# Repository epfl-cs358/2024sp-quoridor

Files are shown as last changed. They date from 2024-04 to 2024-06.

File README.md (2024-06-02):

# 2024sp-quoridor

# Project overview

This project aims to create a modified version of the physical board game called Quoridor, a strategic maze-building game, where a player competes against a computer opponent on the board. <br> 
Quoridor is a 2 player game where each player’s piece start on opposite sides of the board, each turn the player chooses to either move their piece in any cardinal direction (up, down, left, right) or place a wall to block the other player’s path (walls cannot be moved once placed), the first player to get to the other side wins. 

# Project Proposal link:

https://docs.google.com/document/d/114cAhuUHxiCxB0LIXvpHFLx6ZjFtf0oyKlaDsvuiIQ8/edit?usp=sharing

# Project instructions
These instructions are structured in 2 sub-assemblies:
- The Gripper
  
- The machine
  - Main part
  - Y axis rail
 
As well as a set of instructions for the Computer Vision:
- Players and walls detection
- Game board and coordinates building

The two sub assemblies can be built in parallel and assembled at the end. The design is such that only two screws hold the gripper to the rest of the assembly, so it's quite easy to modify the gripper seperately.

# Gripper
## Overview:
Here is the design of the gripper for the Quoridor game board.
The gripper's movements include rotation (±280°), translation (10 cm), and gripping (4 cm wide). The gripper is powered by two DMS15 motors and one Servo 9G, with a power supply of 5V from an external source, drawing a maximum of 3A.

Gripper CAD

Gripper CAD Back

Gripper CAD

Gripper CAD

Gripper CAD

## Required Components:
Motors:
- 2x DMS15 Servo
- 1x 9G Servo

Bearings:
- 2 dry bearings (outer diameter: 10mm, inner diameter: 8mm)
- 1 standard bearing (outer diameter: 24mm, inner diameter: 15mm)
- 2 Metal Shafts 100x8mm

Tools: File, lubricant, screwdriver

Equipment: 3D printer, laser cutter (for plates of 5mm and 3mm thickness, or alternatively, these parts can be 3D printed) 

## Assembly Instructions:
#### Gripper Assembly:

1. Clean the gear and the two racks with the file.
2. Attach the claws to the claw racks using screws (two screws per claw). Ensure the screws are tightened sufficiently to prevent any movement.
3. Mount the gear onto the servo. Apply a bit of force to fit it securely and then screw it in place (Note: This servo is trash).
4. Slide the two claws onto the rack holder, positioning them close together.
5. Use an Arduino to run the servo, setting it to its maximum position (180° = closed).
6. Slide the servo on top of the rack holder. Adjust the claws slightly to ensure the teeth align correctly (this step may require some patience, precision and despair).
7. Optional: you can stick pieces of rubber on the gripper clamp to increase adhesion (I used pieces of rubber glove).

Gripper CAD
Gripper CAD
Gripper CAD
Gripper CAD

#### Moving Part:

1. Clean the bearing holder and the main linear part.
2. Insert the bearing and nuts into the bearing holder.
3. Mount the servo on top of the bearing holder.

Gripper CAD

5. Insert the two dry bearings and nuts into the main linear part.
6. Position the servo with the bearing holder underneath the main linear part.
7. Secure the assembly by adding screws to the top of the main linear part. Use a small screwdriver to access the holes.
8. Slide the rack under the rack holder.
9. Attach the rack holder to the back of the main linear part, ensuring the rack holder protrudes upwards.

#### Main Part:

1. Try to pass the 2 metal axes through the two laser-cut 5mm parts. If necessary, use a file to clean the holes, but do not over-file as the axes need to stay securely in place.
2. Place the left and right pillar supports on the 5mm main plate. You can add screws for additional stability, but this is not mandatory.
3. Position the two upper pillar fix on top of the pillar spacers and screw them in place.
4. Place nuts on the right pillar support and the linear servo support, then screw them onto the main plate.
5. Attach the servo circular extender (I dont know how to call that) to the main gear and secure it using the screws provided with the servo.
6. Insert the two metal axes, slide the moving part onto them, and add the two spacers at the top.

Gripper CAD

8. Position the servo motor and the two pillars, then add screws at the top and base to secure them.
9. Run the two servos with an Arduino, ensuring the rotation is set to 0 and the linear position is also at 0.
10. Attach the main lower plate to the main plate using spacers.
11. Slide the moving part to the top and fix the gear onto the servo motor. The goal is to have the last teeth of the rack engaged by the gear. (Optional: It is recommended to screw it only when everything is installed).
12. Return to the claw assembly. Fix the gripper support servo to the bearing, applying a bit of force to secure it, and add the screws provided with the servo.
13. Insert the servo from the claw into the gripper support servo, ensuring the cables are passed through before positioning the servo. 
14. Add two screws to secure everything. (Optional: It is recommended to do this only when everything is installed and tested to avoid damaging the claw).

## Wiring:

Due to their high power consumption, all 3 servos must be powered by an external power source of at least 5v/3amp.
Here is the electrical diagram to connect them to a Ramps 1.6



1 is the gripper servo, 2 is the rotation servo and 3 is the servo of the linear actuator.

Wiring
Wiring
Wiring

## Improvements:

- The 9G servos are unreliable and prone to malfunction. Consider using higher-quality or bigger servos to improve the performance and longevity of the gripper.

# Machine sub-assembly



# 3D printed parts

## Camera mount
- 1x main part
- 1x camera clamp


## Walls

- 10x in red
- 10x in blue

  Print in this direction to get the best results (no supports necessary)
2024-05-30-134702_1920x1080_scrot

## Player pawns

- 1x in red
- 1x in blue

## Board

- 2x "long"
  

- 1x "square"
  

- 1x "little square"
  

## Angle brackets
- 15x
2024-05-30-134950_1920x1080_scrot

## Corner brackets

Warning, these are symetrical pieces !
One of each
2024-05-30-135919_1920x1080_scrot

## End pulley

- 2x


## Optionnal : 3D printed T-nuts

The metallic openbuilds t-nuts are recommended. We 3d printed those because we forgot to order them. We ended up doing a slightly modified version of the original openbuilds CAD model with a bigger diameter, that works better when 3d printing
2024-05-30-135202_1920x1080_scrot

# Laser cutting

## In MDF

## Main board
- 1x Main board, 10mm

## Walls holder
- 2x, 3mm

## In acrylic

## Camera arms
- 2x, 5mm 


## Wheel plate
-3x 3mm
2024-05-30-143234_1920x1080_scrot

## Stepper mount plate
-2x 3mm


## End pulley bracket

- 4x 3mm (Two are used per axis)


## What needs improvements

3mm thick acrylic is not strong enough. We had a failure for an end pulley bracket, the 3d printed part ended up stronger.
signal-2024-05-30-124640

We also a noticed a crack developing on one of the wheel plate
signal-2024-05-30-124415

# Assembly instructions

With all the parts cut and printed, we are ready for assembly (note that you can also 3d print as you go, since the three pieces for the board for example take quite long to print)

First, screw in the wall holders pieces to the board. These parts add thickness to the board, so doing this first helps stabilizing it a bit more (MDF tends to bend with time).
2024-05-30-140227_1920x1080_scrot

Next, screw in the 8 angle brackets to the board (4 on each side).


Attach the V slot aluminium profiles, screwing them in place with the t-nuts

Screw in the corner brackets. These help stabilizing the profiles, and at the end to mount the camera arms.


Now flip the board upside down, with the top side of the profile resting on your workspace. We will use the profile as spacer.
Slide in the 3d printed boards part. Glue them. gravity will hold them in place. We used fast super-glue, but with this setup you can use a glue that takes a while to set.


## X axis assembly (built this seperately)

Warning : follow precisely this order, so you don't need to dissassemble sub-assemblies down the line

Mount the wheels to the wheel plate (this is the plate we will later mount the gripper to)
Slide the wheels+plate assembly to the middle of the profile.

Mount the end pulley plates on both side on end of the profile


Mount the stepper mounting plate on the other side
WhatsApp Image 2024-05-30 at 15 28 48

Mount the angle bracket to the v-slot. The placement is simple : on each end,  they are next to each other, sarting at the end of the profile.

### Do this two times, for both sides:

Mount the wheels to the plate and then slide the assembled carriage.



## Combine x axis assembly with the rest
Now we can mount the stepper on the x axis with the belt. Attach the belt to the plate going above the profile like this:

signal-2024-05-30-131015

Slide in the end switch mount. Tighten it so it does not move, but don't try to be precise with regards to the adjustments. Adjustements are done when everything is in place.

9f54f568-a379-4a69-852f-7c88d7756aae

Attach the Y stepper to the stepper motor plate, setup the belt but don't attach it to the gripper plate yet.

Put the gripper assembly on top of the plate, screw it in place


Screw in the electronic box.
Put the arduino+ramps+motor driver sandwich inside of it. Do the wiring according to the diagram. Pass the cables via the side holes (otherwise you won't be able to close the lid at the end).

335123297-452fb32d-1a28-4367-88d5-c3750ed1e14c (1) (1) (1)

## Camera arms

1. Screw in the arms to the angle brackets
WhatsApp Image 2024-05-30 at 14 55 10

2. Connect bot arms together


3. Mount the camera using the clamp
e45bf986-da7e-4e04-8ccc-194e948133e6

## Button

1. Screw in the button housing to the board
2. screw the button itself to the housing from below



## The end

Congratulation ! At this point, you should have the full machine assembled like this:


You can now proceed with adjustements regarding the end switch positioning, as well as the camera angle for the webcam.

# Arduino code 
The arduino code is separated in 2 parts, one is for all movements on the board (the X, Y axis stepper motors and 3 servo motors for the gripper) and the part is for communication and interpreter which will send, receive and decode message from the computer which it will translate to valid moves on the board. <br> <br>

The arduino will be managing communication with itself and the computer with a serial connection.
This diagram shows the communication between all of our components: <br> <br>


The arduino will send a "end turn" message through the serial once the button pressed, then the computer will communicate with the camera to detect the current board state (placement of the player pieces and the walls), with that it will compute the best move for the bot. Finally it will send the move information as the board position of the piece we want to grab, the new board position where we want to place the piece, the piece type, and optionally the orientation of the piece if it is a wall. <br> <br>

To accomplish the first part the arduino will stay idle, but once the player presses the end turn button it will trigger an interrupt. This will cause the arduino to print the message "get next move", which will be sent by the serial port. <br> <br>
Then the arduino will remain idle until it receives the move information from the computer.<br>
There are 2 types of moves, moving a player piece or a wall piece.
If the move is to move a player piece, then the move information will be under this form: <old_position><new_position><player> where old_position and new_position are board position for player pieces which are shown here:

<br> 
If the move is to move a wall piece, then the move information will be under this form: <old_position><new_position><wall><old_orientation><new_orientation> where old_orientation new_orientation are either horizontal or vertical, and old_position and new_position are board position for wall pieces which are shown here:

With all of this information the arduino knows what it has to do.<br> <br> 

Now for actually placing the piece where it needs to go. <br>
First we must move to the piece we desire to move, which we use the 2 X and Y stepper motors. Since the board was made with cells that are 4 times bigger than the gap between cells, it just takes knowing the distance in steps from the position 0 0 of the grabber to board position 00 for a player piece, and the distance in steps from a board position to a neighboring one board position to know how to move any board position for player pieces and wall pieces.<br>
That is the hard part done, then the gripper drops down, grabs the piece, pulls it back up, rotates it if it is needed (for instance if we had to place a vertical wall), moves to the new position, drops down, releases the piece, goes back up and moves back to its origin.<br><br>
Here are some videos that process working flawlessly:
<video src="https://github.com/epfl-cs358/2024sp-quoridor/assets/125994939/afad0169-728d-4bf2-bb4c-040145c0d592" controls></video>
<video src="https://github.com/epfl-cs358/2024sp-quoridor/assets/125994939/391f769e-7cd7-4f65-ab67-2949c7b72846" controls></video>

<br>

# Quoridor Solver
We implemented a greedy version of a Quoridor solver.
The solver sees the game as a graph where:
  - each board cell is vertex (with a board position attached to it).
  - each possibility of movement from one cell to another is represented by an edge from that vertex to the other.
  - each wall is represented by missing edges from 2 cells to 2 other cells.
<!--stop list--> 
The solver works as follows:
  - computes the shortest path to get to the other side for both players, it uses a breadth first search algorithm to do this, as it guarantees that it will find the shortest path first.
  - if the path of the robot is shorter than or equal to the one for the real player
    - then the robot is in an "advantaged" position, thus moves his player piece one step forward on its shortest path
  - otherwise it means the path of the robot is longer than the one for the real player
  - the robot is in a "disadvantaged" position, thus it will need to place a wall on the board if it wants to win
  - if the robot has 0 free walls to move:
    - there is nothing it can do to win, thus moves his player piece one step forward on its shortest path
  - else
    - for each wall position that goes on the real player's previously calculated shortest path:
      - checks that there is no colision with other walls on that board position
      - calculates the shortest path for both players on that new board with that wall placed
      - checks that there is a path to a winning cell for both players
      - keeps state of the best "winning move" and the best "losing move"
      - the best "winning move" is defined as the move that maximizes the distance difference between the robot's and player's new path where the robot's new path is the shorter one.
      - the best "losing move" is defined as the move that minimizes the distance difference between the robot's and the player's new path where the robot's new path is the longer one.
    - if a "winning move" exists:
      - it moves a free wall to the position in the best winning move
    - else
      - it moves a free wall to the position in the best losing move
<!--stop list-->
The solver seems quite robust and plays really well, but it still has some weaknesses due to the fact that it uses a greedy algorithm which means that it only considers the best move for itself on this turn. <br> 
So no future planning or strategy is going on and it won't consider what the real player can do in their future moves.

# Computer Vision
## Pieces detection
The playing pieces (players and walls) are recognized through color detection.

Using colorimetry software, we first get the BGR (Blue Green Red) color of each of the playing pieces we need to detect. This value, along with the camera feed, is then converted into the HSV (Hue, Saturation, Value) format. We now create a color mask based on the detected color with a range on the hue based on a sensitivity chosen to be 50 to account for the shadows and slight color variations.

Once we obtain this mask, we use OpenCV's minAreaRect function to obtain all the possible rectangles containing objects of the same color. We then apply filters to only keep the rectangles for which the height and width would correspond to our playing pieces. This is also how we distinguish between walls and player pieces since their enclosing rectangles would have different sizes.

Once we filter the rectangles of the correct sizes, we extract the centers of these rectangles which we then use to detect their coordinates on the grid. This part will be explained on the next section.

Finally, for the walls, we also need to detect their orientation. We do that using the "angle" value returned by the minAreaRect function and by comparing the width and height of the rectangle. Just the angle is not enough in our case since the openCV function returns a value between 0° and 90°,it is very error-prone when thresholding between Horizontal and Vertical values (if the value is slightly above 90°, it goes back again to 1°).

## Game board
The board, its cells, and wall gaps are not detected as is, but rather re-created after detecting the board's corners.
Each corner is uniquely identified by ArUco markers: they are a sort of QR code that can be generated and identified through its corresponding library.
Given the corners and the cells' number and dimensions, a grid is recreated: <br>
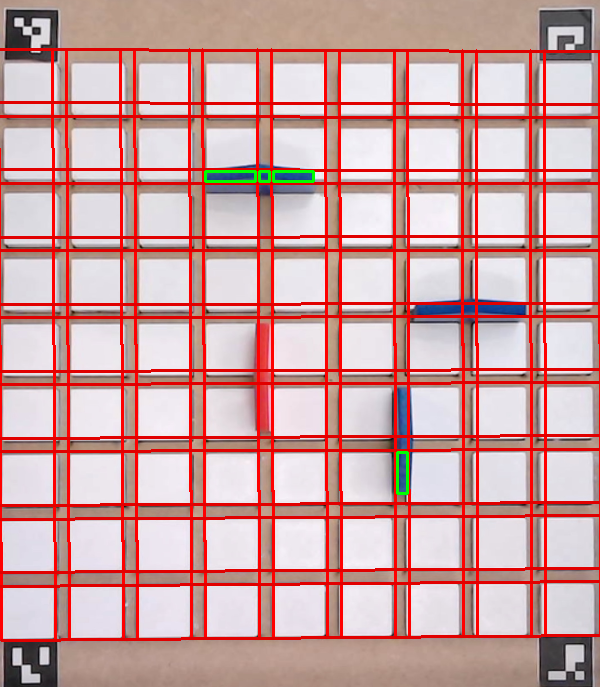
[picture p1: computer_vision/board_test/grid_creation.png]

<br> <br>
You can see in the picture that the grid is purposefully offset near the top. Because the camera is not directly centered on top of the board, walls near the top will tend to look like they are higher on the board than they truly are.
You will find more detail on aruco detection and perspective wrapping in the code /computer_vision/create_grid.py <br>
When creating the grid, the set of intersections between all perpendicular grid lines is stored for future use. For each intersection, we store the absolute coordinates as well as the game-system coordinates (9 units on each side, origin is bottom left) <br>
Then, given the absolute coordinates for the pieces' centers, the code uses the set of intersection coordinates to output, for the solver to use, the game-system coordinates of each piece. <br> <br>
When sticking the ArUco markers on the board, you should be mindful that the outer corners should be well-aligned with the board's corners (PS: the markers don't need to have the same size, they should just be well-aligned). <br>
Be careful however that they can be seen entirely from the camera (black square included). Here are corner-case examples: <br>
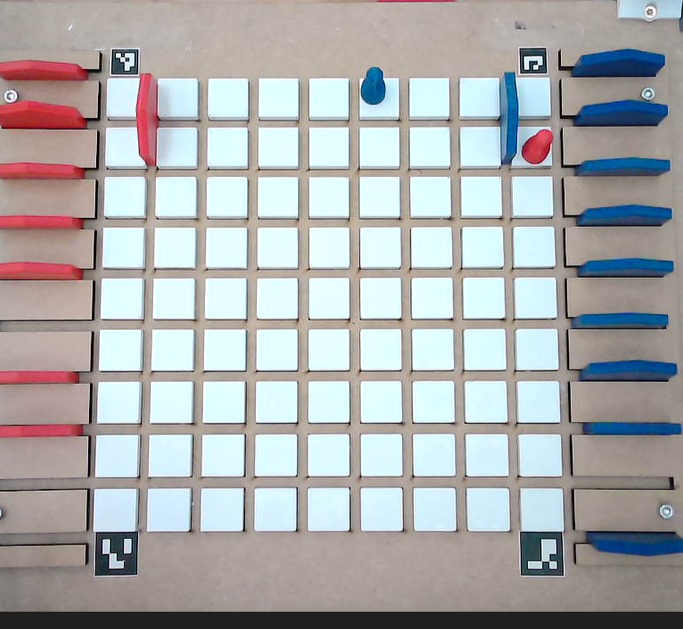
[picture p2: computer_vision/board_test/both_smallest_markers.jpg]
 <br>
On the image above, the top markers should be small enough that the walls placed at the top don't block them
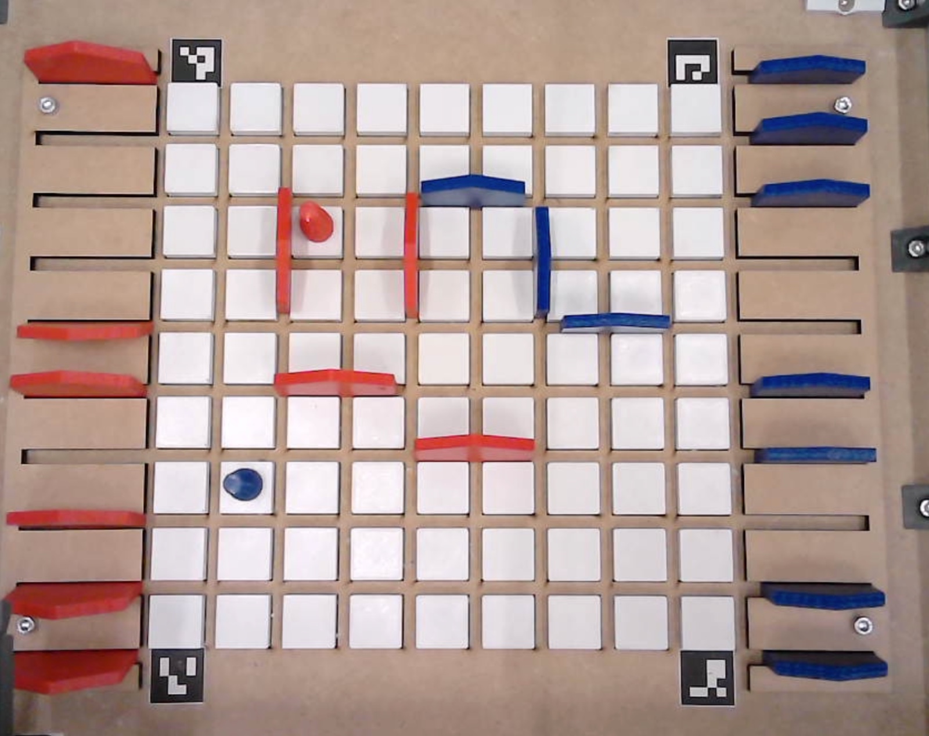
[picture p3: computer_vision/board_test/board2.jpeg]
 <br>
On the image above, the markers are too far down: the black square isn't showing entirely. <br> <br>

# Final Project
And that's it! <br> 
You have successfully built a Quoridor playing robot.<br> 
Now take seat and try to beat your new creation!<br>
<br>
Here you can check out some [videos](https://github.com/epfl-cs358/2024sp-quoridor/tree/main/videos) showing our project's successes (and failures) <br>
<video src="https://github.com/epfl-cs358/2024sp-quoridor/tree/main/videos/video1.mp4" controls></video>
<video src="https://github.com/epfl-cs358/2024sp-quoridor/tree/main/videos/video2.mp4" controls></video>
<video src="https://github.com/epfl-cs358/2024sp-quoridor/tree/main/videos/video3.mp4" controls></video>
<video src="https://github.com/epfl-cs358/2024sp-quoridor/tree/main/videos/video4.mp4" controls></video>

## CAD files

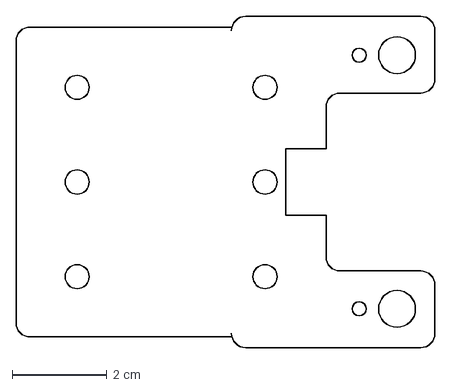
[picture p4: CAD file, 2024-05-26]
Gripper/Laser Cutting/Main plate.dxf
8.85 x 7.00 cm

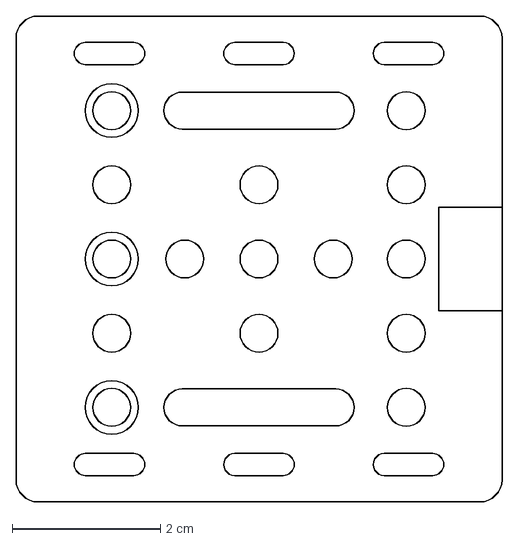
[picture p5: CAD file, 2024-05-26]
Gripper/Laser Cutting/Main Lower Plate.dxf
6.55 x 6.55 cm

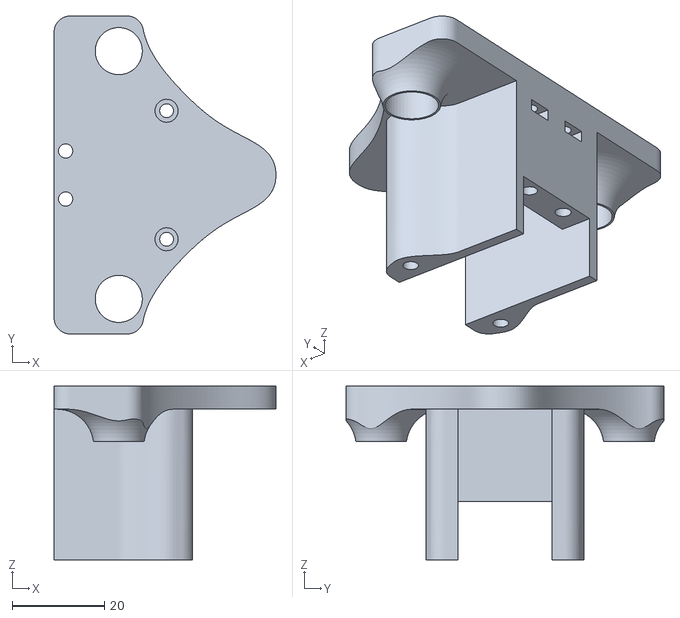
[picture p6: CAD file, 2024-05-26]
Gripper/3D Printing/Main Part Linear.stl
48.0 x 68.8 x 37.6

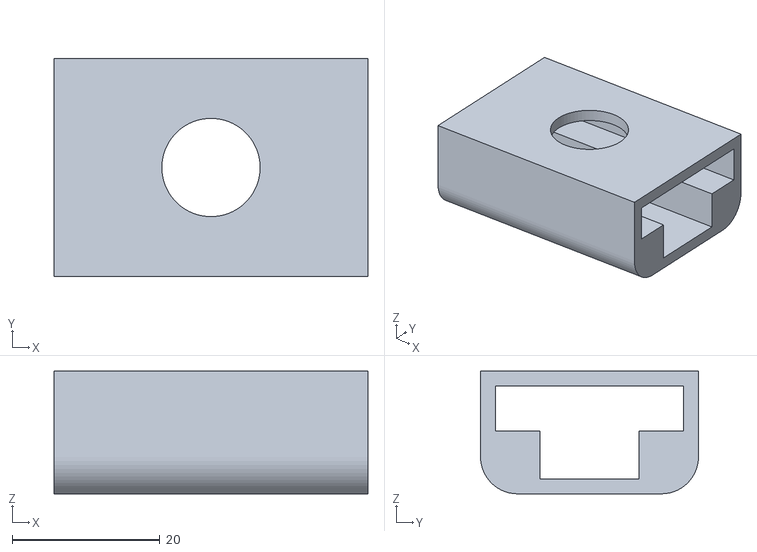
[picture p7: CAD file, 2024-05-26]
Gripper/3D Printing/Claw/Support Gripper Rack.stl
42.5 x 29.5 x 16.6

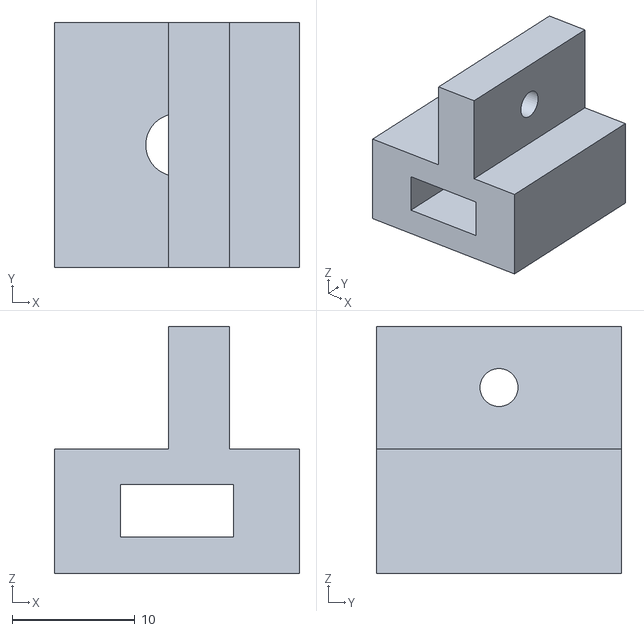
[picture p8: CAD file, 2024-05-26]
Gripper/3D Printing/Support Right Pillar.stl
20.0 x 20.0 x 20.2

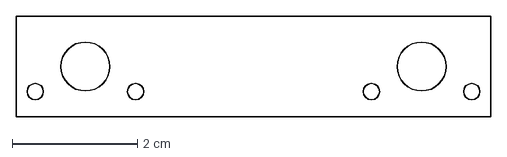
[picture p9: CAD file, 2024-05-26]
Gripper/Laser Cutting/Spacer Pillar.dxf
7.56 x 1.60 cm

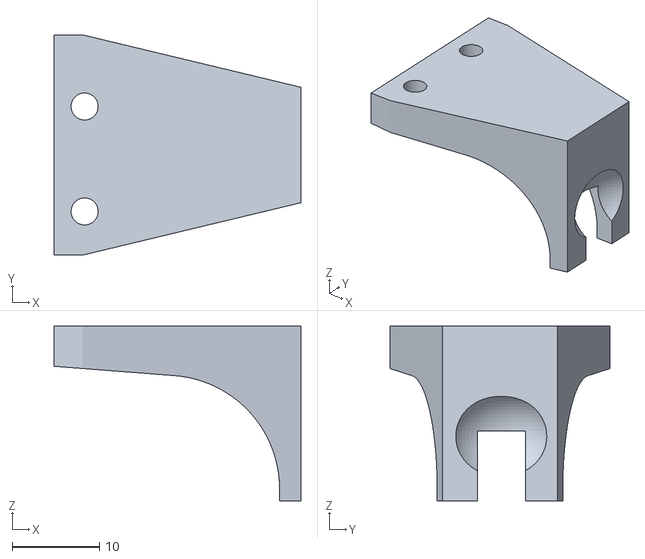
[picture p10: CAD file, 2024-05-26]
Gripper/3D Printing/Claw/Gripper Claw x2.stl
28.2 x 25.2 x 20.0

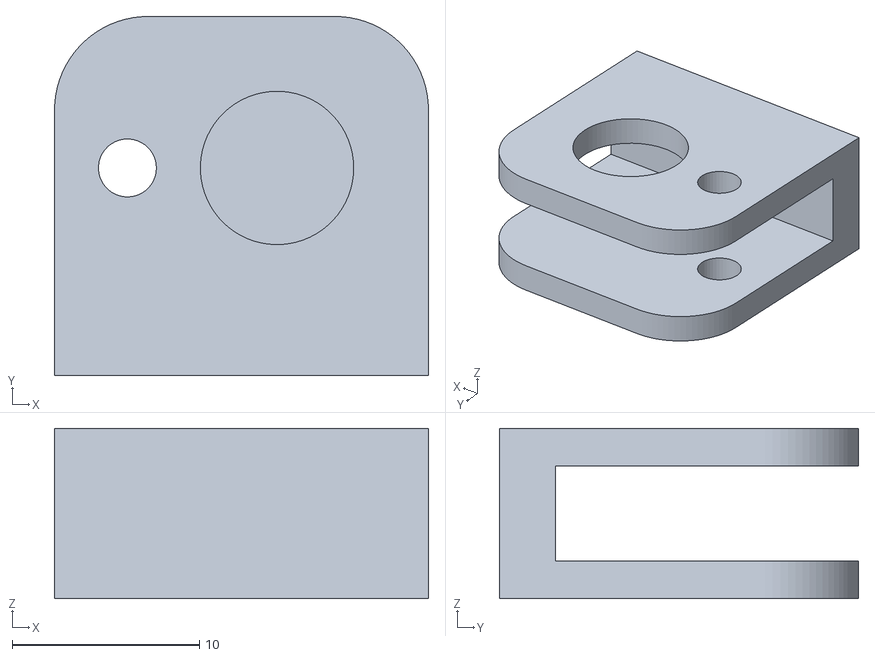
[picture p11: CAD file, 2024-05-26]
Gripper/3D Printing/Limit Lower Left Axis.stl
20.0 x 19.2 x 9.10

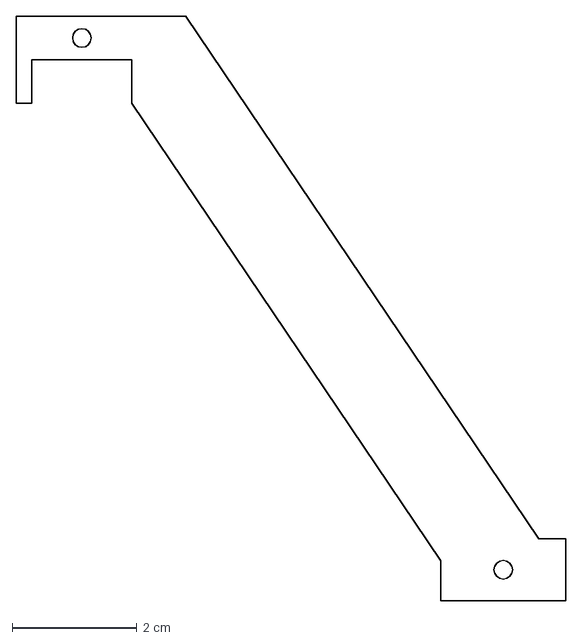
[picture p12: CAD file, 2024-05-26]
Gripper/Laser Cutting/Pillar Right.dxf
8.81 x 9.38 cm

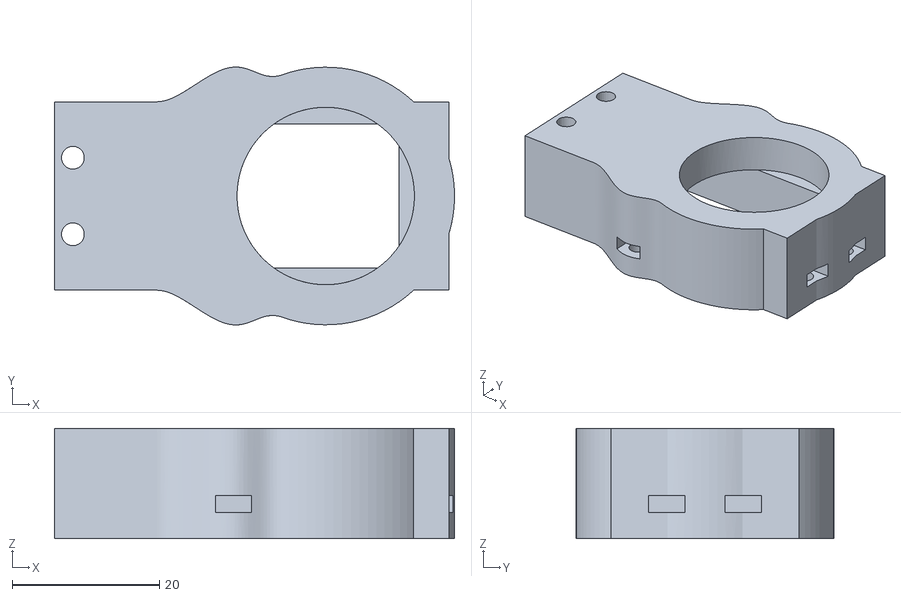
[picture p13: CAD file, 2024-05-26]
Gripper/3D Printing/Bearing Support Rotation.stl
54.3 x 35.0 x 15.0

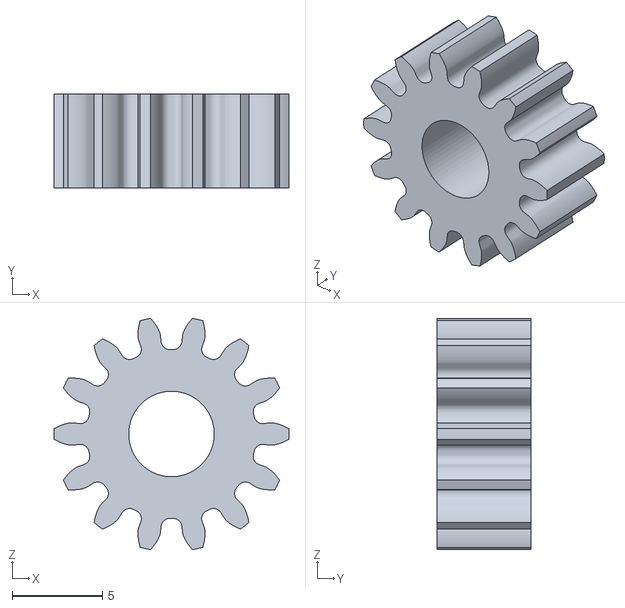
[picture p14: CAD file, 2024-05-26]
Gripper/3D Printing/Claw/Gear Gripper.stl
13.1 x 5.20 x 12.8

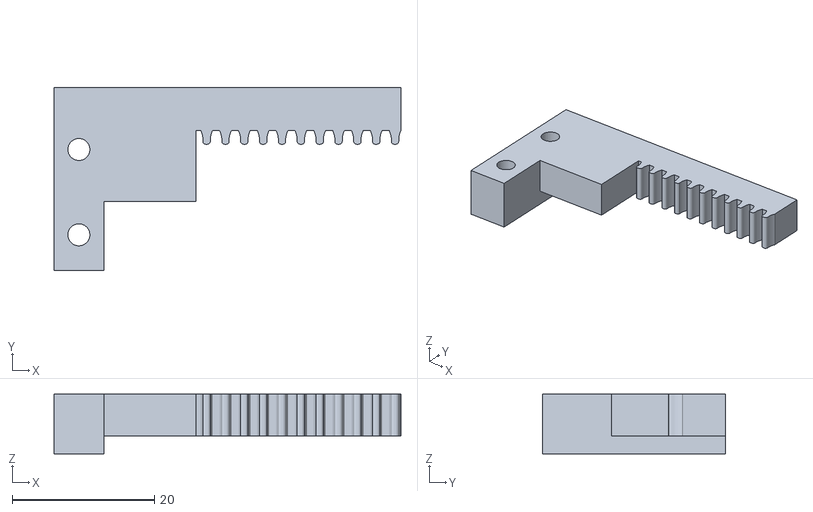
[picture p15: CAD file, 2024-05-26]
Gripper/3D Printing/Claw/Rack Slider x2.stl
48.8 x 25.7 x 8.40

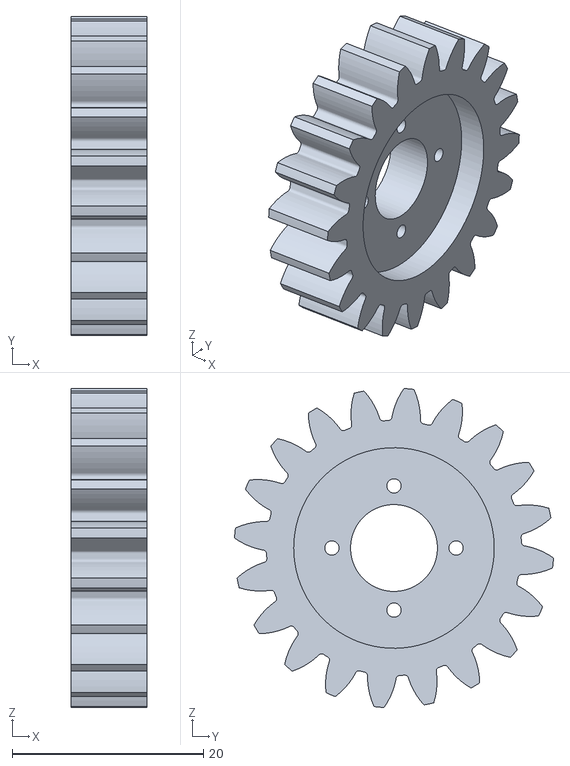
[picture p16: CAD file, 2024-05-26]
Gripper/3D Printing/Gear Linear.stl
8.00 x 33.4 x 33.4

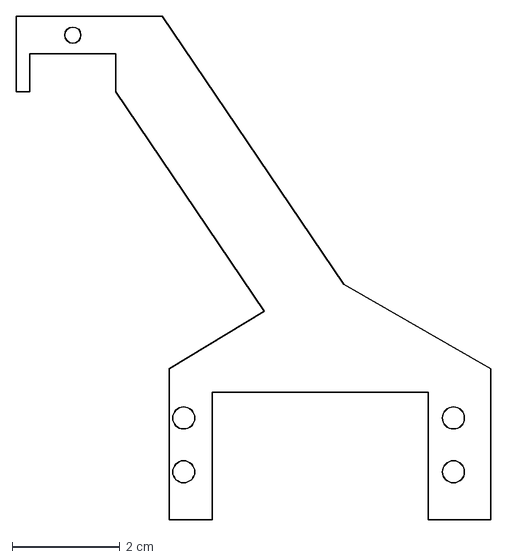
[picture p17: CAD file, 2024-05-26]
Gripper/Laser Cutting/Pillar Left.dxf
8.81 x 9.35 cm

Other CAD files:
Gripper/3D Printing/Claw/Support Gripper Servo.stl
Gripper/3D Printing/Upper Pillar Fix x2.stl
Gripper/3D Printing/Spacer x2.stl
Gripper/3D Printing/Limit Lower Right Axis.stl
Gripper/3D Printing/Rack.stl
Gripper/3D Printing/Support Servo Linear.stl

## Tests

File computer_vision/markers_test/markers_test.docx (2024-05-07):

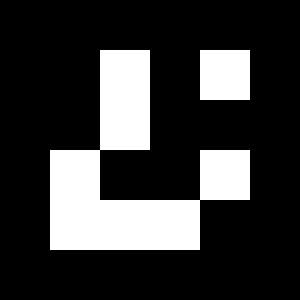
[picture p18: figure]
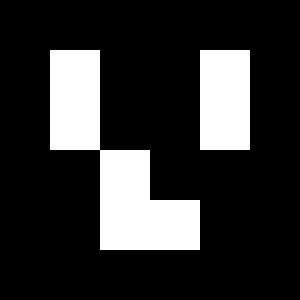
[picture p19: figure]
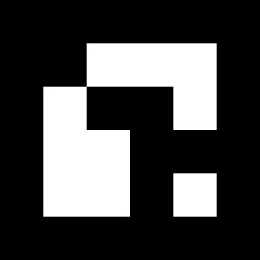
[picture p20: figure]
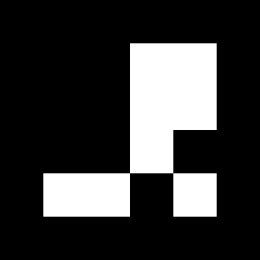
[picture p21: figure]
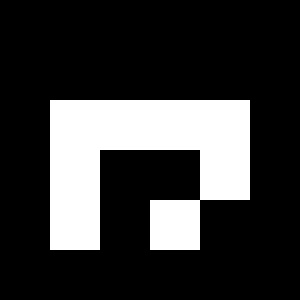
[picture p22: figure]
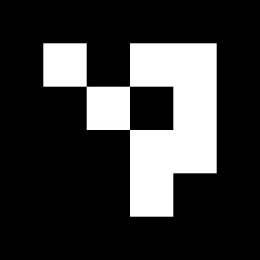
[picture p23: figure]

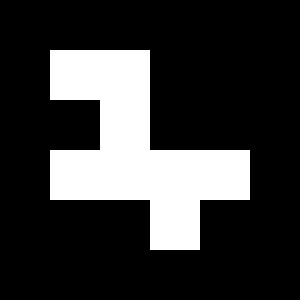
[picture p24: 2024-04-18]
computer_vision/markers_test/marker_7.jpg

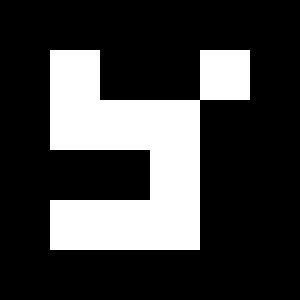
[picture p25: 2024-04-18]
computer_vision/markers_test/marker_6.jpg

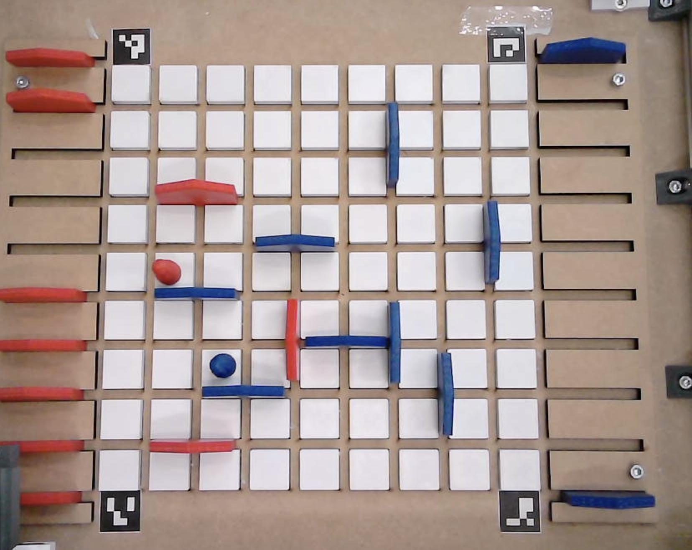
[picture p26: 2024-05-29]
computer_vision/board_test/image.png

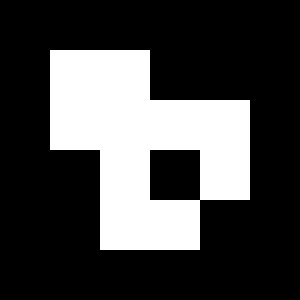
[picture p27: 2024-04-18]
computer_vision/markers_test/marker_9.jpg

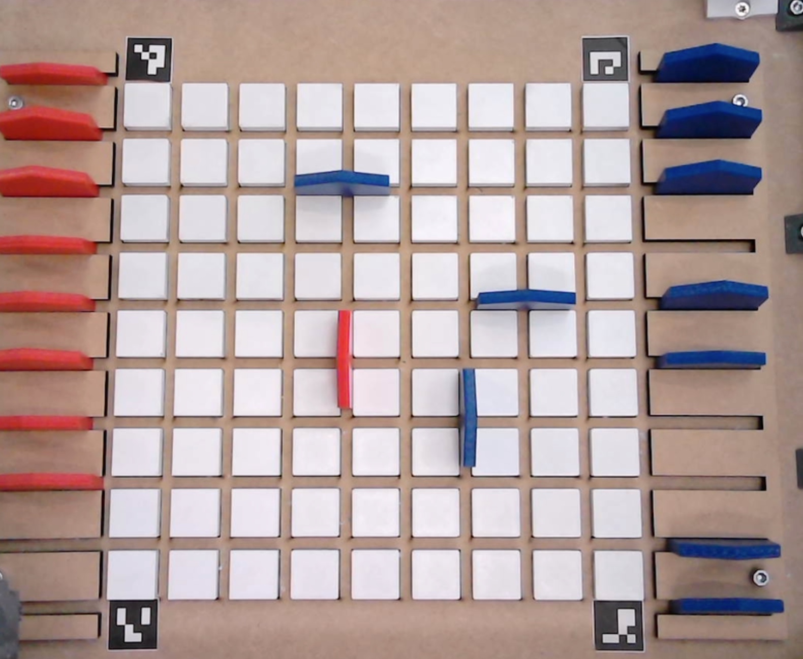
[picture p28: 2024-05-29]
computer_vision/board_test/board4.jpeg

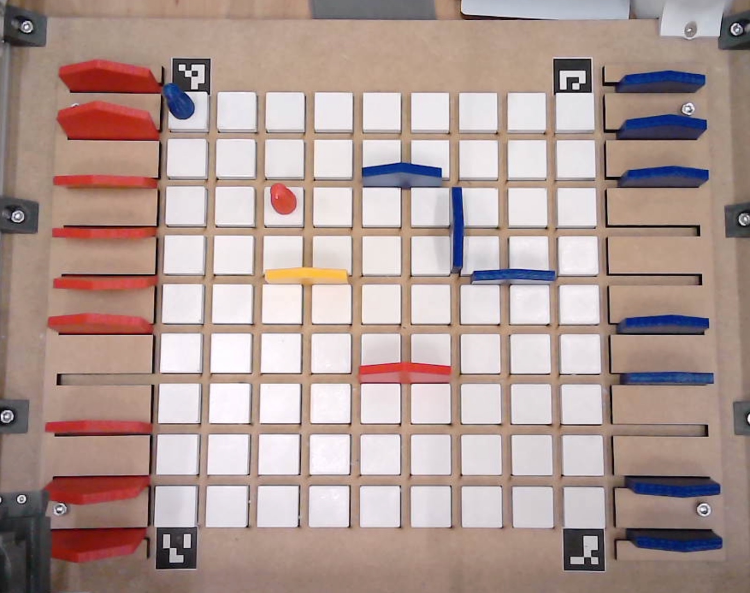
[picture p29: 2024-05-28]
computer_vision/board_test/board.jpeg

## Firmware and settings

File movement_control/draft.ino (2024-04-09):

#include <AccelStepper.h>
#include <MultiStepper.h>
// Voor de Arduino Uno + CNC shield V3
#define MOTOR_X_ENABLE_PIN 8
#define MOTOR_X_STEP_PIN 2
#define MOTOR_X_DIR_PIN 5


#define MOTOR_Y_ENABLE_PIN 8
#define MOTOR_Y_STEP_PIN 3
#define MOTOR_Y_DIR_PIN 6
#define SPEED 200
#define ACCELERATION 1
#define SIZE 400
AccelStepper motorX(1, MOTOR_X_STEP_PIN, MOTOR_X_DIR_PIN);
AccelStepper motorY(1, MOTOR_Y_STEP_PIN, MOTOR_Y_DIR_PIN);
MultiStepper steppers;

void setup()
{
   pinMode(MOTOR_X_ENABLE_PIN, OUTPUT);
   pinMode(MOTOR_Y_ENABLE_PIN, OUTPUT);

   motorX.setEnablePin(MOTOR_X_ENABLE_PIN);
   motorX.setPinsInverted(false, false, true);
   motorX.setAcceleration(ACCELERATION);
   motorX.setMaxSpeed(SPEED);
   motorX.setSpeed(SPEED);
   motorX.enableOutputs();

   motorY.setEnablePin(MOTOR_Y_ENABLE_PIN);
   motorY.setPinsInverted(false, false, true);
   motorY.setAcceleration(ACCELERATION);
   motorY.setMaxSpeed(SPEED);
   motorY.setSpeed(SPEED);
   motorY.enableOutputs();

  steppers.addStepper(motorX);
  steppers.addStepper(motorY);
   
   long positions[2]; 

  positions[0] = 3*SIZE;
  positions[1] = 2*SIZE;
  delay(3000);
  steppers.moveTo(positions);
  steppers.runSpeedToPosition();
  delay(3000);
}

void loop()
{
}

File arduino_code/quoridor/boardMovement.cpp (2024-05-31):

#include <Servo.h>
#include <AccelStepper.h>
#include <MultiStepper.h>
#include "boardMovement.h"
#include "boardUtils.cpp"

AccelStepper X(
  AccelStepper::DRIVER, 
  StepperXPin1, 
  StepperXPin2
);
AccelStepper Y(
  AccelStepper::DRIVER, 
  StepperYPin1, 
  StepperYPin2 
);
MultiStepper XY;
long pos_xy[2] = {0,0};

bool isClawHigh = true;
bool isClawClose = false;
WallOrientation clawOrientation = HORIZONTAL;

//range servo black : 270°
//range command : 0-180°
// 0°   = 0°
// 90°  = 65°
// 180° = 125°


Servo linearServo;
Servo rotationServo;
Servo gripperServo;

int linearPos = 0;
int rotationPos = 0;
int gripperPos = 0;

//Speed
int linearSpeed = 10;
int rotationSpeed = 10;
int gripperSpeed = 10;

//Starting position
int linearStart = 130;
int rotationStart = 0;


//End position
int linearEnd = 10;
int linearMid = 75;
int rotationEnd = 125;

//gripper position
int gripperFullOpen = 100;
int gripperMidOpen = 130;
int gripperClose = 180;
int gripperWall = 160;
int gripperPawn = 165;

void downMid(){
  for (linearPos; linearPos >= linearMid; linearPos -= 1) {
    linearServo.write(linearPos);
    delay(linearSpeed);
  }
  delay(100);
}

void downFull(){
  for (linearPos; linearPos >= linearEnd; linearPos -= 1) {
    linearServo.write(linearPos);
    delay(linearSpeed);
  }
  delay(100);
}

void upFull(){
    for (linearPos; linearPos <= linearStart; linearPos += 1) {
    linearServo.write(linearPos);
    delay(linearSpeed);
  }
  delay(100);
}

void upMid(){
    for (linearPos; linearPos <= linearMid; linearPos += 1) {
    linearServo.write(linearPos);
    delay(linearSpeed);
  }
  delay(100);
}

void rotate(int angle){
  if(angle > rotationPos){
    for (rotationPos; rotationPos <= angle; rotationPos += 1) {
      rotationServo.write(rotationPos);
      delay(rotationSpeed);
    }
  }else{
    for (rotationPos; rotationPos >= angle; rotationPos -= 1) {
      rotationServo.write(rotationPos);
      delay(rotationSpeed);
    }
  }
  delay(100);
}

void grabWall(){
    for (gripperPos; gripperPos <= gripperWall; gripperPos += 1) {
    gripperServo.write(gripperPos);
    delay(gripperSpeed);
  }
  delay(500);
}

void grabPawn(){
    for (gripperPos; gripperPos <= gripperPawn; gripperPos += 1) {
    gripperServo.write(gripperPos);
    delay(gripperSpeed);
  }
  delay(100);
}

void openMid(){
  for (gripperPos; gripperPos >= gripperMidOpen; gripperPos -= 1) {
    gripperServo.write(gripperPos);
    delay(gripperSpeed);
  }
  delay(100);
}


void closeMid(){
  for (gripperPos; gripperPos <= gripperMidOpen; gripperPos += 1) {
    gripperServo.write(gripperPos);
    delay(gripperSpeed);
  }
  delay(100);
}

void openFull(){
  for (gripperPos; gripperPos >= gripperFullOpen; gripperPos -= 1) {
    gripperServo.write(gripperPos);
    delay(gripperSpeed);
  }
  delay(100);
}

void setupGrabber() {
  gripperServo.write(gripperClose);
  delay(100);
  gripperPos = gripperClose;

  linearServo.write(linearStart);
  linearPos = linearStart;
  delay(100);
  rotationServo.write(0);
  rotationPos = 0;
  delay(100);

  linearServo.attach(11);
  gripperServo.attach(6);
  rotationServo.attach(5);

  //Set the gripper to the right starting position
  //openMid();
  upFull();
  rotate(0);

  delay(1000);
}

void setupMotors() {

  X.setMaxSpeed(CALIBRATION_SPEED);
  X.setAcceleration(Acceleration);
  X.setEnablePin(StepperXPin3);
  X.setPinsInverted(false, false, true);
  X.enableOutputs();

  Y.setMaxSpeed(CALIBRATION_SPEED);
  Y.setAcceleration(Acceleration);
  Y.setEnablePin(StepperYPin3);
  Y.setPinsInverted(false, false, true);
  Y.enableOutputs();

  XY.addStepper(X);
  XY.addStepper(Y);

  setupGrabber();

  Serial.begin(9600);
  delay(1000);
  Serial.println("START");
}

void forceStopMotors(){
  X.stop();
  Y.stop();
  X.disableOutputs();
  Y.disableOutputs();
}

void moveToXY(long x, long y){
  pos_xy[0] = x;
  pos_xy[1] = y;
  XY.moveTo(pos_xy);
  XY.runSpeedToPosition();
}

void goToOrigin(){
  moveToXY(0, 0);
}

bool validPlayer(BoardPosition pos){
  return 0 <= pos && pos / 10 <= 8 && pos % 10 <= 8;
}

bool validWall(BoardPosition pos){
  return 0 <= pos && (pos / 10 <= 7 && pos % 10 <= 7 || pos % 10 == 8);
}
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

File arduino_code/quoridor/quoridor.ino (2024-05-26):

#include "boardMovement.h"
#include "serialInterpreter.h"


#define NORMAL_RUN 0

//#define DEBUG_MOVE 1

//USE THESE PINS FOR INTERUPT MANAGEMENT
#define NextMovePin 18
#define StopPin 19

bool isWaitingForResponse = false;

void stopISR(){
  forceStopMotors();
  while(1){}
} 

void nextMoveISR(){
  if(!isWaitingForResponse){
    Serial.println("Get next move");
    isWaitingForResponse = true;
  }
}

void setupInterrupts(){
  //pinMode(StopPin, INPUT_PULLUP);
  //attachInterrupt(digitalPinToInterrupt(StopPin), stopISR, RISING);

  pinMode(NextMovePin, INPUT_PULLUP);
  attachInterrupt(digitalPinToInterrupt(NextMovePin), nextMoveISR, RISING);
}

void setup() {
  setupMotors();
  // Calibration sequence
  calibrateMotors();
  #ifdef NORMAL_RUN
   setupInterpreter();
   setupInterrupts(); 
  #endif
  #ifdef DEBUG_MOVE
   debugStartMotors();
  #endif
}


void loop() {
  #ifdef DEBUG_MOVE 
   motorControlLoop(); 
  #endif

  #ifdef NORMAL_RUN
    if(isWaitingForResponse){
      waitingForResponseLoop();
      isWaitingForResponse = false;
    }
  #endif
}

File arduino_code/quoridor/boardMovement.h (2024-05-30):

#include <stdint.h>

//https://reprap.org/forum/read.php?219,168722 as stated here
//TODO PUT CORRECT PINS FOR STEPPER AND SERVOS
#define StepperXPin1 54
#define StepperXPin2 55
#define StepperXPin3 38

#define StepperYPin1 60
#define StepperYPin2 61
#define StepperYPin3 56

#define Speed 20 //1400
#define Acceleration 20 //9000

#define XMinStopPin 3
#define YMinStopPin 14
#define CALIBRATION_SPEED 1400
#define CALIBRATION_STEP 5

#define ServoClawPin 1
#define ServoRotationPin 1
#define ServoZPin 1

enum PieceType {WALL, PLAYER};
enum WallOrientation{VERTICAL, HORIZONTAL};
typedef uint8_t BoardPosition;
typedef struct{
  BoardPosition old_position;
  BoardPosition new_position;
  PieceType piece_type;
  WallOrientation old_orientation;
  WallOrientation new_orientation;
}MoveData; 

void setupMotors();
void forceStopMotors();

void playMove(MoveData move_data);
void moveToBoardPosition(BoardPosition pos, PieceType type);
void openClaw();
void closeClaw(PieceType type);
void rotateTo(WallOrientation orientation);
void lowerClaw(PieceType type);
void raiseClaw(PieceType type);

void debugStartMotors();
void motorControlLoop();
void calibrateMotors();

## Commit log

2024-04-09 stepper move testing script
2024-04-19 camera feed
2024-04-23 add arduino code for quoridor interpreter
2024-04-30 code works on board
2024-05-06 calibration sequence added, to be tested
2024-05-06 calibration wroks
2024-05-10 CV for pieces and board merged together
2024-05-13 add gripper code
2024-05-13 add gripper motor code
2024-05-13 change gripper pinout
2024-05-13 fused the grabber with the Arduino code
2024-05-17 CV: new board detection
2024-05-21 add CAD + documentation for the gripper
    [Bearing Support Rotation.stl, Gear Gripper.stl, Gear Linear.stl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]
2024-05-21 Modif doc Gripper
2024-05-28 CV: correct board representation
2024-05-30 fixed calibration
2024-05-30 new full quoridor code + calibration for the arduino
2024-05-30 calibration added
2024-05-31 Able to display camera_output live
2024-05-31 added arduino code to readme
